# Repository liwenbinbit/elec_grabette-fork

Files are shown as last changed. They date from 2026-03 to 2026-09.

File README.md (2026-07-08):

# "Grabette"/"Gripette" Electronic Boards

This repository is part of the ["Grabette" project](https://github.com/pollen-robotics/grabette). It gathers several small PCBs of Grabette/Gripette. 

## Grabette
Grapette is the data acquisition side.

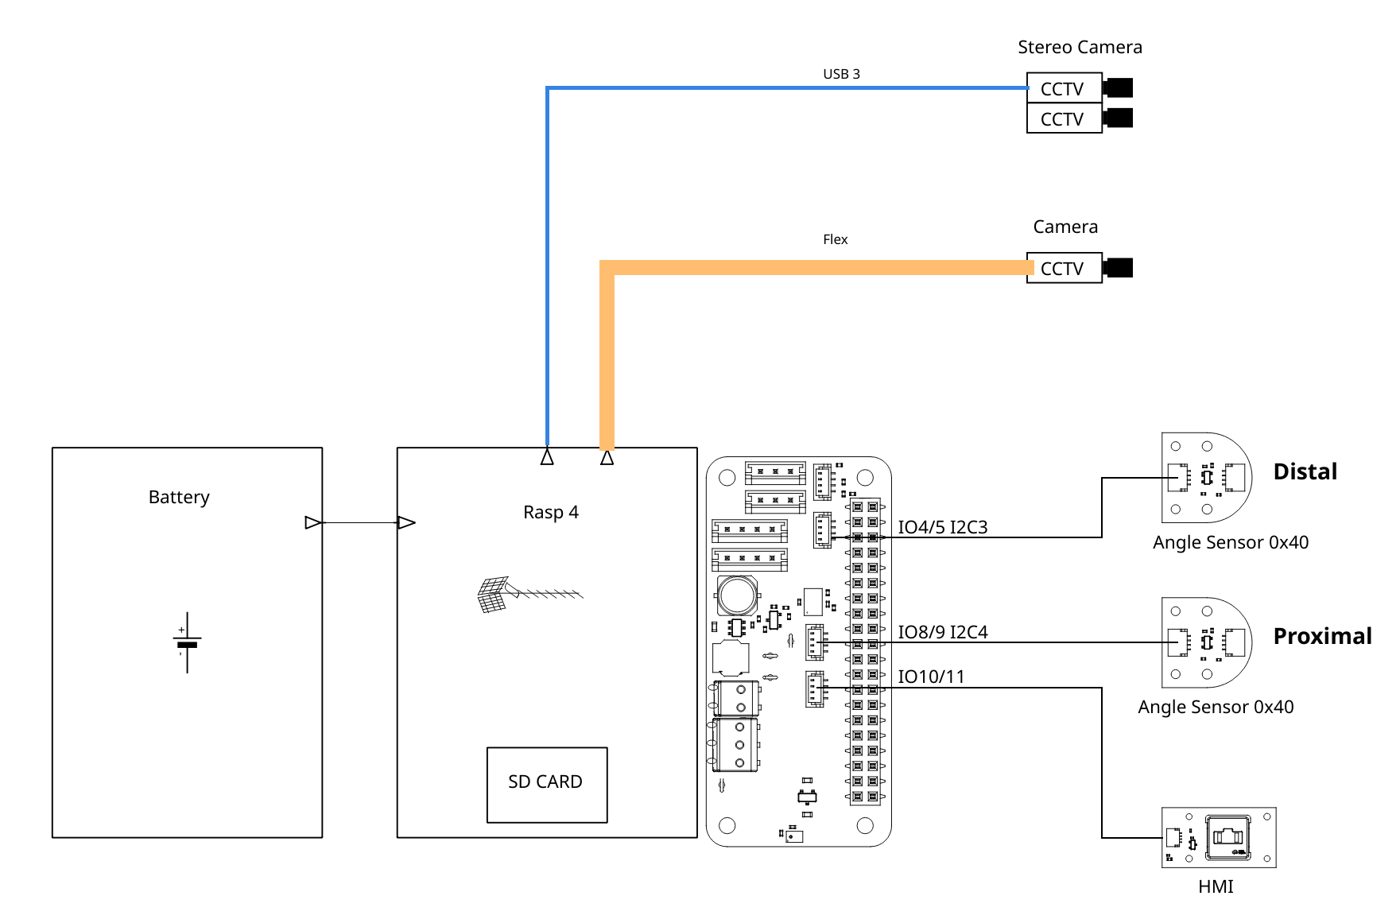
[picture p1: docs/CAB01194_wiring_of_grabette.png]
grabette wiring


It is based on a battery-powered Raspberry PI 4 plus a [HAT](https://github.com/pollen-robotics/elec_RPI_Robot_HAT) to which a serie of sensing elements is added. Camera, Stereo Camera, angle sensors, IMU (included on the HAT) and a button + a LED as user interface.

 - angle_sensor

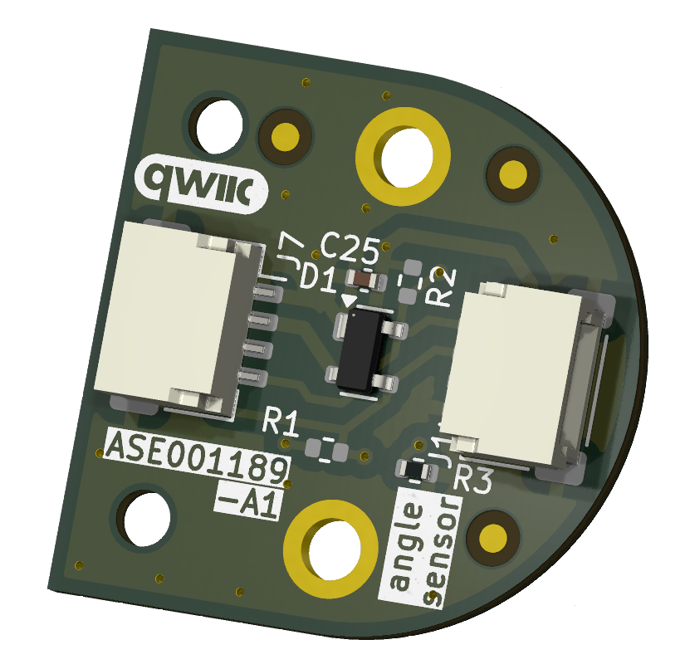
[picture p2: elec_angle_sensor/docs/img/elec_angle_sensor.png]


 - IMU (Not used)

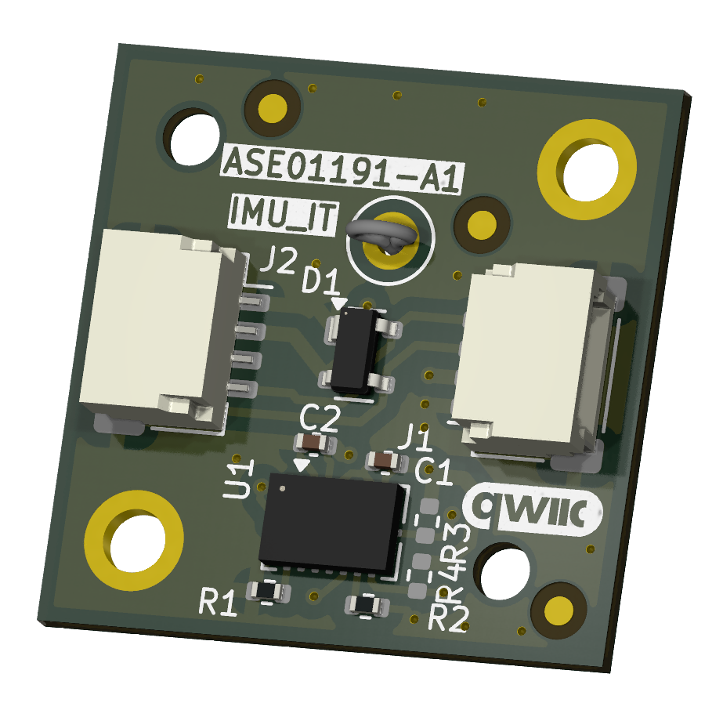
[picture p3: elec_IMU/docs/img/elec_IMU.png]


 - HMI

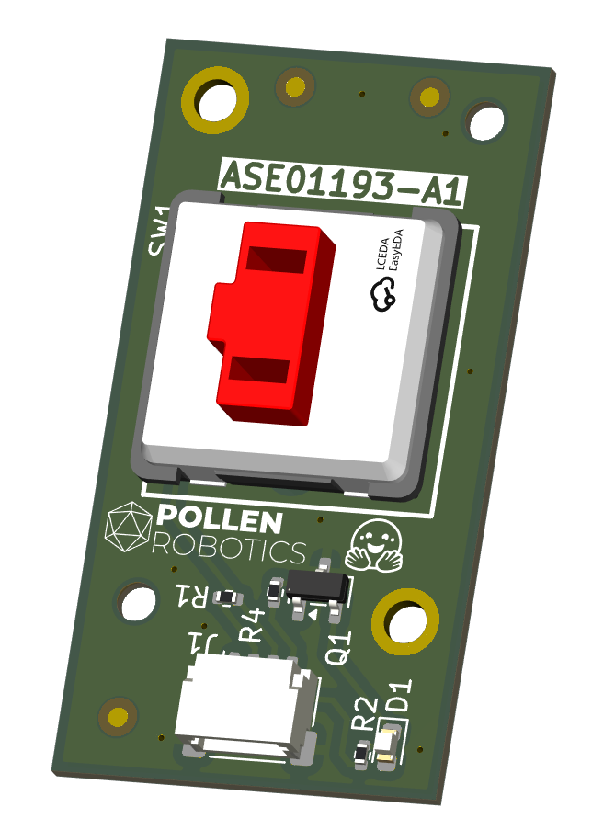
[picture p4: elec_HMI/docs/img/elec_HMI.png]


## Gripette
Gripette is the actuator side. 

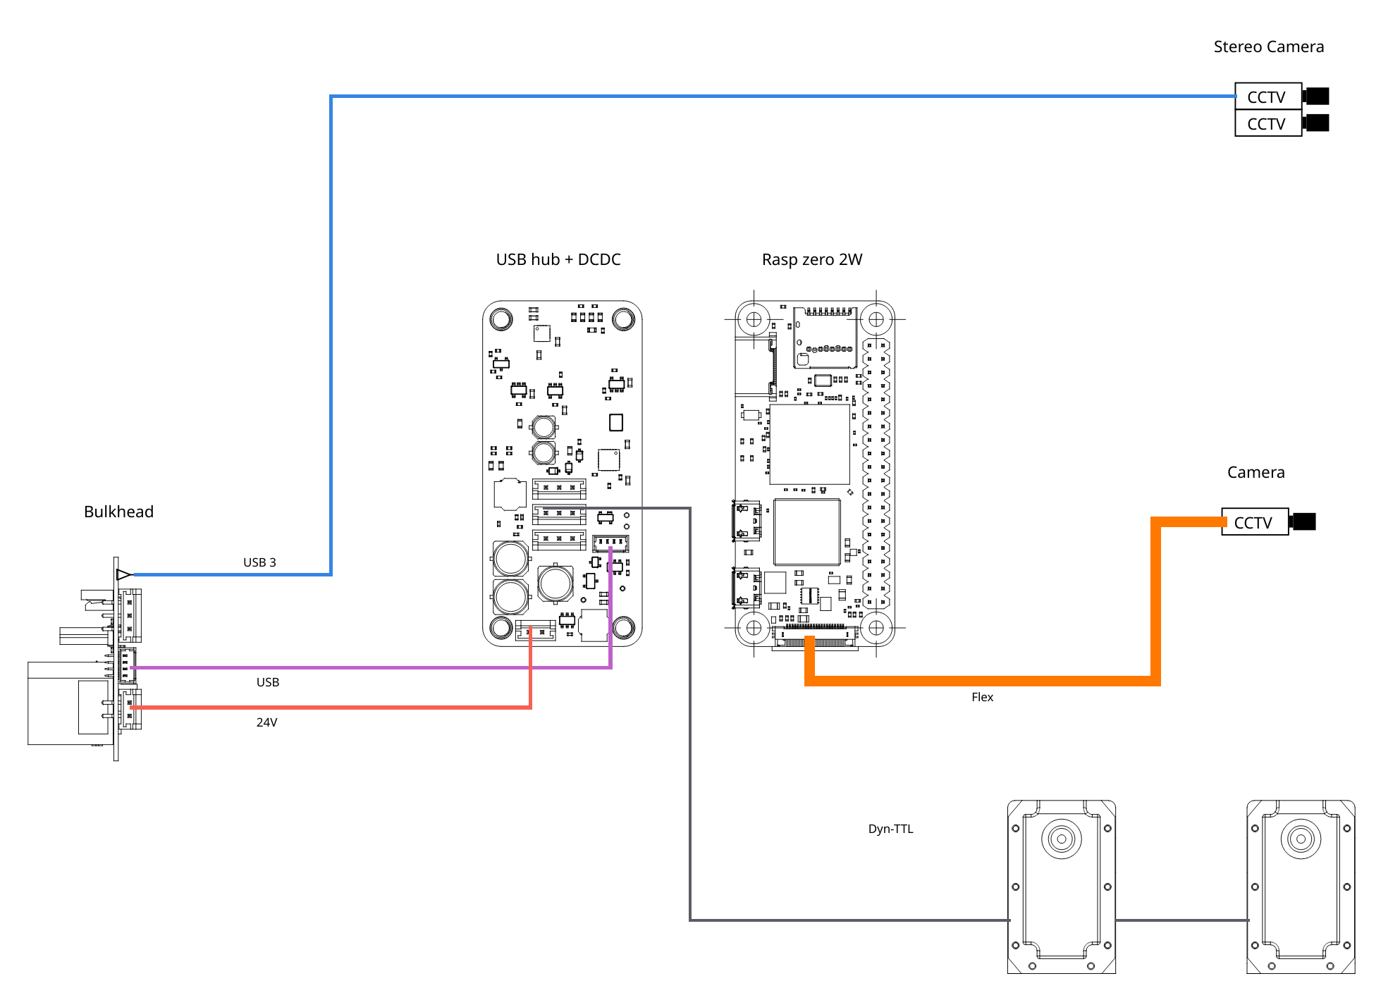
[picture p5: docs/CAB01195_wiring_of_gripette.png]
gripette wiring


It also gathers data with the same Camera/Stereo Camera system and drive motors. The "under-HAT" electronic board is associated to a Raspberry PI zero 2W. It has a interface to the motors (now Feetech wiring). A Bulk-head board makes the mechanical interface with the arm that holds Gripette.

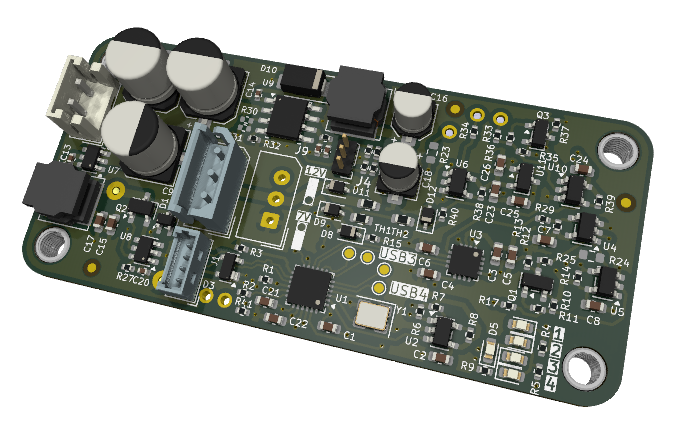
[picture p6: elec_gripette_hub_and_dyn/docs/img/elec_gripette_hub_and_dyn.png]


Bulk-head:

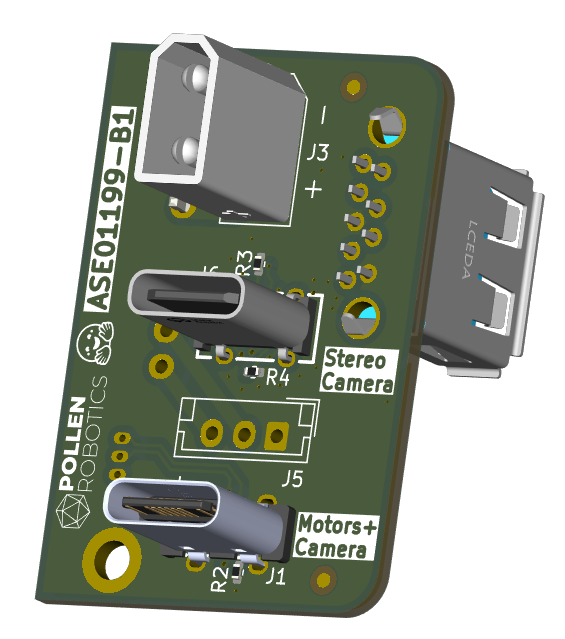
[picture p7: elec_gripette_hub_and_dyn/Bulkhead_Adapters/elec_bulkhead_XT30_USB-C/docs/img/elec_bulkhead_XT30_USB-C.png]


## Basically
 - Designed with KiCAD 9.

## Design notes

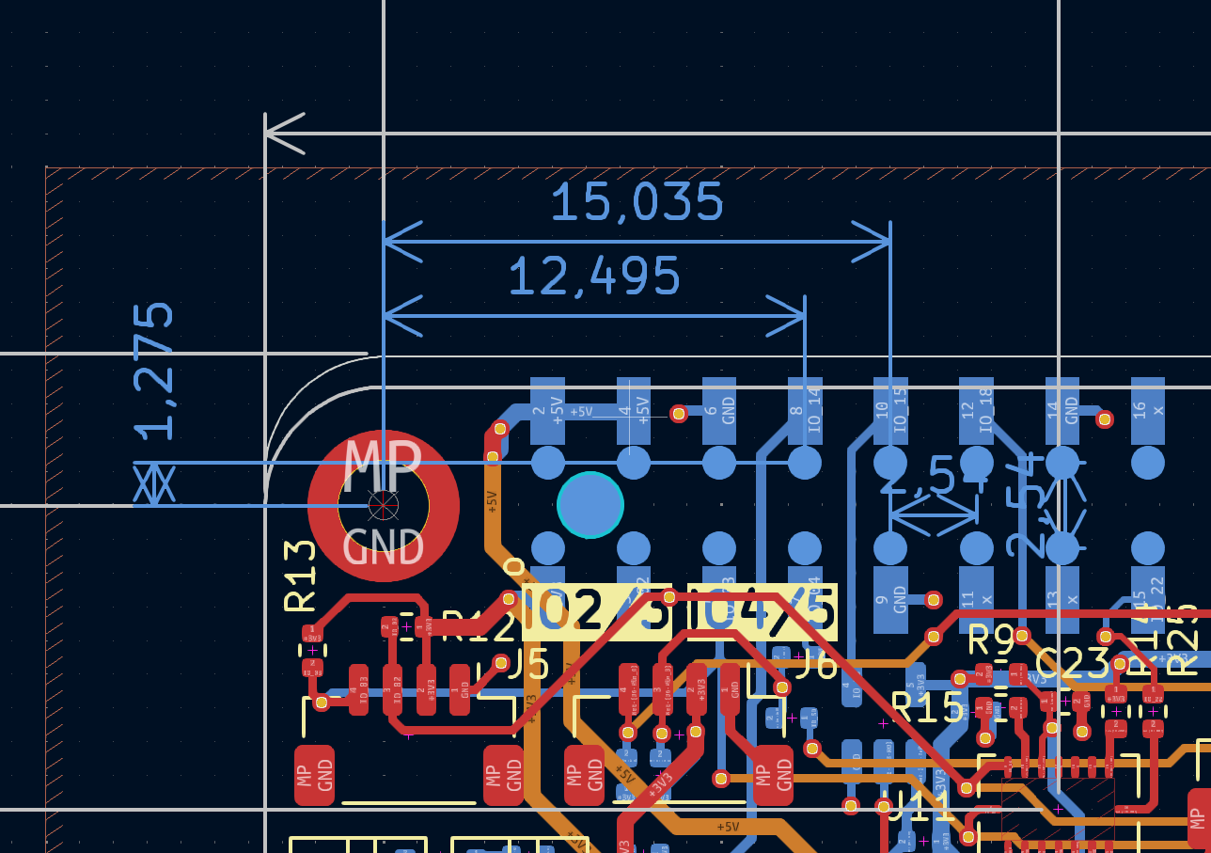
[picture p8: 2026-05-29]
elec_gripette_hub_and_dyn/docs/extra_pogo-pins_positions.png

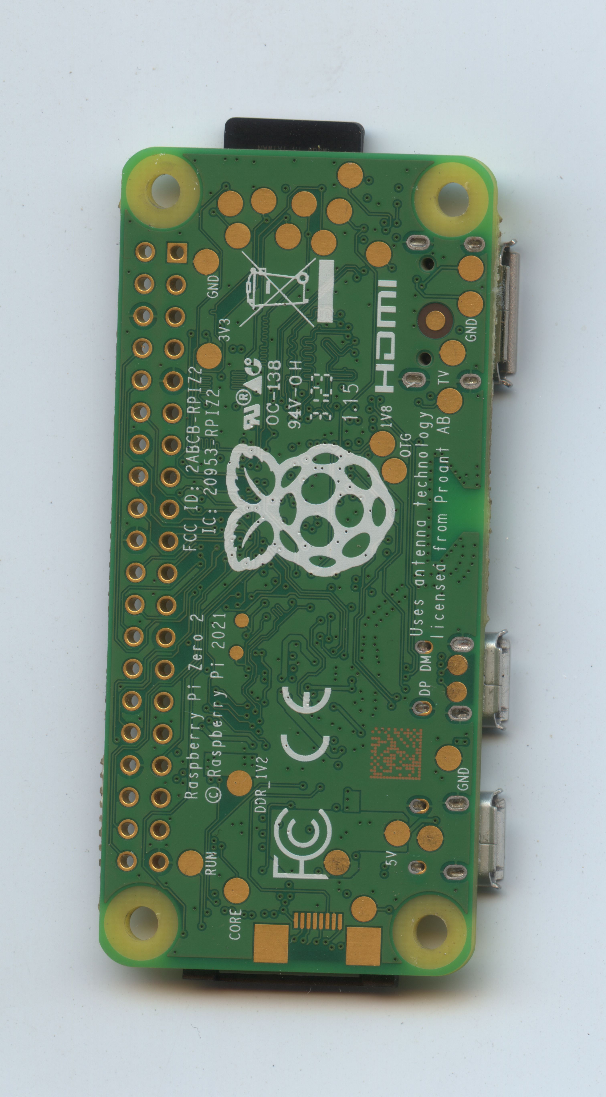
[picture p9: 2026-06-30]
elec_gripette_hub_and_dyn/docs/rasp_zero_2W_bottom.jpg

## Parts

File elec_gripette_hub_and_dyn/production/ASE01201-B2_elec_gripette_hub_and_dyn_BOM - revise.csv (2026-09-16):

Designator | Footprint | Quantity | Value | LCSC Part #
C1 | 0603 | 1 | 10u | C1691
C10, C11, C9 | CP_Elec_6.3x7.7 | 3 | 10u 35V | C72488
C12 | 0402 | 1 | 4n7 | C1518204
C13, C14 | 0402 | 2 | 100n | C307331
C15, C17 | 0603 | 2 | 22u 6V3 | C84419
C16, C18 | CP_Elec_4x5.4 | 2 | 22u 16V | C72502
C19 | 0402 | 1 | 47p | C1567
C2, C21, C22, C23, C24, C4, C6, C7, C8 | 0603 | 9 | 100n | C85864
C20 | 0402 | 1 | 100n 6V3 | C1525
C25, C26, C3, C5 | 0603 | 4 | 1u | C1592
C27 | 0805 | 1 | 3,3u 35V | C361184
D1 | SOT-323_SC-70 | 1 | BAT54W | C78606
D10 | D_SMA | 1 | D_Schottky 3A | C8678
D11, D9 | D_SOD-323 | 2 | B5819WS | C64886
D12, D8 | D_SOD-323 | 2 | 5V1 | C151348
D2, D4, D6, D7 | 0603 | 4 | LED_Small | C7429915
D3 | SOT-143 | 1 | SP0503BAHT | C41364459
D5 | 0603 | 1 | LED_Small | C19171301
H4, H5, H6, H7 | SMD_BD5.6-D4.1_spacer | 4 | M2,5 x 4mm spacer | C2916324
J1 | Molex_PicoBlade_53047-0410_1x04_P1.25mm_Vertical | 1 | pico4 | C504989
J10, J13, J14 | CONN-TH_YZ95315064P-01_pogo | 3 | Pogo-pin 4mm | C5157245
J2 | JST_EH_B2B-EH-A_1x02_P2.50mm_Vertical | 1 | JST EH 2 | C160262
J4 | PinHeader_1x03_P1.27mm_Vertical | 1 | Header 3 | C7470079
J5 | Molex_SPOX_5267-03A_1x03_P2.50mm_Vertical | 1 | Feetech | C293315
J7, J8 | CONN-TH_YZ08415060P-02_pogo | 2 | Pogo-pin 2A 4mm | C7471674
L1, L2 | L_Bourns_SRN6045TA | 2 | 6,8u 3A | C57254
Q1, Q3 | SOT-23 | 2 | MMBT3906 | C727128
Q2 | TSOT-23 | 1 | SI2312CDS-T1-GE3 | C142518
R1, R10, R11, R13, R14, R35, R36, R38, R39, R8 | 0402 | 10 | 10k | C25744
R12, R37 | 0402 | 2 | 20k | C2906867
R15, R40 | 0402 | 2 | 150R | C138054
R16 | 0402 | 1 | 100k | C2906883
R17, R2, R25, R29, R33, R34, R41 | 0402 | 7 | 0R | C17168
R18 | 0402 | 1 | 16k9 | C25858
R21 | 0402 | 1 | 62k | C2909375
R22 | 0402 | 1 | 8k2 | C25924
R26 | 0402 | 1 | 7k5 | C25918
R27 | 0402 | 1 | 100R | C2906860
R28 | 0603 | 1 | 0R | C21189
R3 | 0402 | 1 | 2k7 | C138017
R32 | 0402 | 1 | 243k | C43249
R4, R5, R9 | 0402 | 3 | 330R | C105875
R6, R7 | 0402 | 2 | 5k1 | C25905
TH1, TH2 | 0603 | 2 | 100R thermistor | C913703
U1 | WQFN-24-1EP_4x4mm_P0.5mm_EP2.6x2.6mm | 1 | FE1.1s_24-Pin_WQFN | C6776948
U10, U5 | SOT-23-5 | 2 | SN74LVC1G126DBVR | C7834
U11 | SOT-23 | 1 | MCP1700x-330xxTT | C39051
U2 | SOT-23-5 | 1 | 24C02S | C18723540
U3 | WCH_QFN-16-1EP_3x3mm_P0.5mm_EP1.8x1.8mm | 1 | CH343P | C2846043
U4, U6 | SOT-23-5 | 2 | SN74LVC1G125DBV | C23654
U7 | TSOT-23-6 | 1 | AP63205 | C2071056
U8 | TSOT-23-6 | 1 | LM5050-1 | C473393
U9 | Texas_R-PDSO-G8_EP2.95x4.9mm_Mask2.4x3.1mm_ThermalVias | 1 | TPS54560BDDA | C1850354
Y1 | Crystal_SMD_3225-4Pin_3.2x2.5mm | 1 | 12MHz | C133334

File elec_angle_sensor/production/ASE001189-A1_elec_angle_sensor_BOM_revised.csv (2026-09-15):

Designator | Footprint | Quantity | Value | LCSC Part #
C25 | 402 | 1 | 100n | C307331
D1 | SOT-143 | 1 | SP0503BAHT | C41364459
J1 | JST_SH_SM04B-SRSS-TB_1x04-1MP_P1.00mm_Horizontal | 1 | JST SH | C160404
J7 | JST_SH_SM04B-SRSS-TB_1x04-1MP_P1.00mm_Horizontal | 1 | JST SH | C160404
R3 | 402 | 1 | 0R | C17168
U1 | SOIC-8_3.9x4.9mm_P1.27mm | 1 | AS5600L | C2153666

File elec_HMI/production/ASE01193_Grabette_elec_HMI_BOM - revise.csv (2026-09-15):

Designator | Footprint | Quantity | Value | LCSC Part #
D1 | 0603 | 1 | Red | C84263
J1 | JST_SH_SM04B-SRSS-TB_1x04-1MP_P1.00mm_Horizontal | 1 | JST SH | C160404
Q1 | SOT-23 | 1 | MMBT3906 | C727128
R1 | 0402 | 1 | 10k | C25744
R2, R4 | 0402 | 2 | 470R | C25117
SW1 | SW_Cherry_MX_1.00u_PCB | 1 | SW_SPST | C400229

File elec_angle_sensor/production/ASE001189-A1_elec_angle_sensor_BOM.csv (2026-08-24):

Designator | Footprint | Quantity | Value | LCSC Part #
C25 | 0402 | 1 | 100n | C307331
D1 | SOT-143 | 1 | SP0503BAHT | C41364459
G1 | Logo_qwiic_5mm | 1 | qwiic_Logo
H2 | Logo_HF_2025 | 1 | Logo HF 2025
J1, J7 | JST_SH_SM04B-SRSS-TB_1x04-1MP_P1.00mm_Horizontal | 2 | JST SH | C160404
R1, R2 | 0402 | 2 | DNP-10k | C25744
R3 | 0402 | 1 | 0R | C17168
U1 | SOIC-8_3.9x4.9mm_P1.27mm | 1 | AS5600L | C2153666

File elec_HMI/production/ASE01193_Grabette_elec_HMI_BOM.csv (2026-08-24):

Designator | Footprint | Quantity | Value | LCSC Part #
D1 | 0603 | 1 | Red | C84263
H2 | Logo_HF_2025 | 1 | Logo HF 2025
J1 | JST_SH_SM04B-SRSS-TB_1x04-1MP_P1.00mm_Horizontal | 1 | JST SH | C160404
Q1 | SOT-23 | 1 | MMBT3906 | C727128
R1 | 0402 | 1 | 10k | C25744
R2, R4 | 0402 | 2 | 470R | C25117
SW1 | SW_Cherry_MX_1.00u_PCB | 1 | SW_SPST | C400229

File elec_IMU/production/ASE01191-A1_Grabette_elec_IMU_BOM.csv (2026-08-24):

Designator | Footprint | Quantity | Value | LCSC Part #
C1, C2 | 0402 | 2 | 100n 6V3 | C1525
D1 | SOT-143 | 1 | SP0503BAHT | C41364459
G1 | Logo_qwiic_5mm | 1 | qwiic_Logo
H2 | Logo_HF_2025 | 1 | Logo HF 2025
J1, J2 | JST_SH_SM04B-SRSS-TB_1x04-1MP_P1.00mm_Horizontal | 2 | JST SH | C160404
R1, R2 | 0402 | 2 | 0R | C17168
R3, R4 | 0402 | 2 | DNP-10k | C25744
TP1 | TestPoint_Loop_D2.50mm_Drill1.0mm_LowProfile | 1 | TestPoint
U1 | Bosch_LGA-16_4.5x3mm_P0.5mm_LayoutBorder7x1y_ClockwisePinNumbering | 1 | BMI088 | C194919

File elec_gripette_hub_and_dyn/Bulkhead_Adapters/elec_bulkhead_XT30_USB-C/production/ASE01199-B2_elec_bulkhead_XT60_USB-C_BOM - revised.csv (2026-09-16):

Designator | Footprint | Quantity | Value | LCSC Part #
J1 | USB-C_16p_vert_Shou-Han_TYPE-C 16P LTH6.8 - C5187468 | 1 | USB-C Rec. Vert. | C5187468
J2 | JST_EH_S2B-EH_1x02_P2.50mm_Horizontal | 1 | JST EH 2 | C514173
J3 | AMASS_XT30UPB-M_1x02_P5.0mm_Vertical | 1 | XT30 | C428721
J4 | Molex_PicoBlade_53048-0410_1x04_P1.25mm_Horizontal | 1 | pico4 | C588275
J6 | USB-C_TYPE-C-24PLT-H10.5-1 | 1 | USB_C_Receptacle | C3151750
J8 | USB-A-TH_MOLEX_484080003 | 1 | USB3_A | C587839
R1, R2, R3, R4 | 0402 | 4 | 5k1 | C25905

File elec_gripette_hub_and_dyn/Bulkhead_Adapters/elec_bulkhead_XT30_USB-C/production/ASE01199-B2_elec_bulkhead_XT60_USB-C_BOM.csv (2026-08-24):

Designator | Footprint | Quantity | Value | LCSC Part #
H2 | Logo_HF_2025 | 1 | Logo HF 2025
J1 | USB-C_16p_vert_Shou-Han_TYPE-C 16P LTH6.8 - C5187468 | 1 | USB-C Rec. Vert. | C5187468
J2 | JST_EH_S2B-EH_1x02_P2.50mm_Horizontal | 1 | JST EH 2 | C514173
J3 | AMASS_XT30UPB-M_1x02_P5.0mm_Vertical | 1 | XT30 | C428721
J4 | Molex_PicoBlade_53048-0410_1x04_P1.25mm_Horizontal | 1 | pico4 | C588275
J5 | JST_EH_B3B-EH-A_1x03_P2.50mm_Vertical | 1 | DNP - Dynamixel-3 | C160259
J6 | USB-C_TYPE-C-24PLT-H10.5-1 | 1 | USB_C_Receptacle | C3151750
J8 | USB-A-TH_MOLEX_484080003 | 1 | USB3_A | C587839
J9 | JST_EH_S3B-EH_1x03_P2.50mm_Horizontal | 1 | DNP - Dynamixel-3 | C263754
R1, R2, R3, R4 | 0402 | 4 | 5k1 | C25905

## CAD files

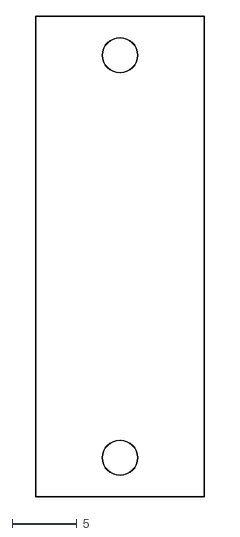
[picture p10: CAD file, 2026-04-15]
elec_gripette_hub_and_dyn/Bulkhead_Adapters/elec_bulkhead_XT30_USB-C/docs/bulkhead.dxf
13.0 x 37.0

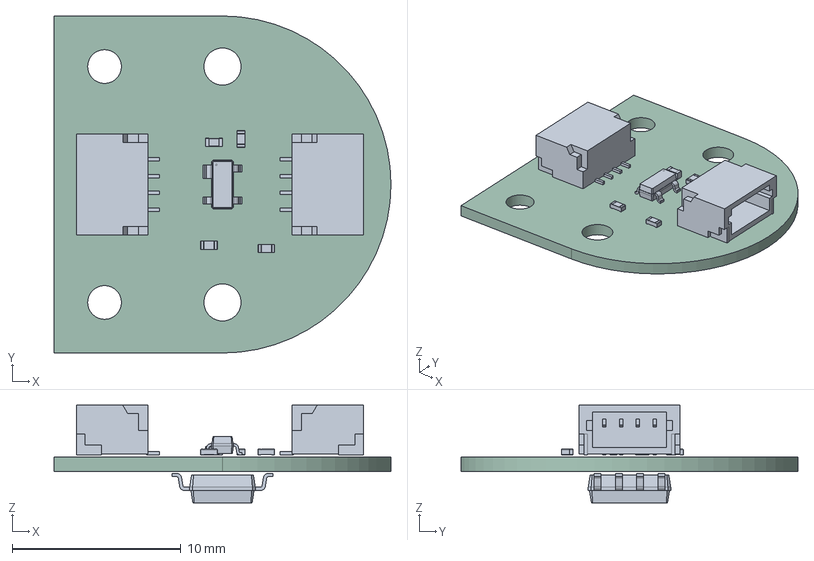
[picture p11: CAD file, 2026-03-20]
elec_angle_sensor/production/ASE001189-A1_elec_angle_sensor_STEP.step
20.0 x 20.0 x 5.79 mm
C_0402_1005Metric
JST_SH_SM04B-SRSS-TB_1x04-1MP_P1.00mm_Horizontal x 2
R_0402_1005Metric x 3
SOT-143
SOIC-8_3.9x4.9mm_P1.27mm
elec_angle_sensor_PCB

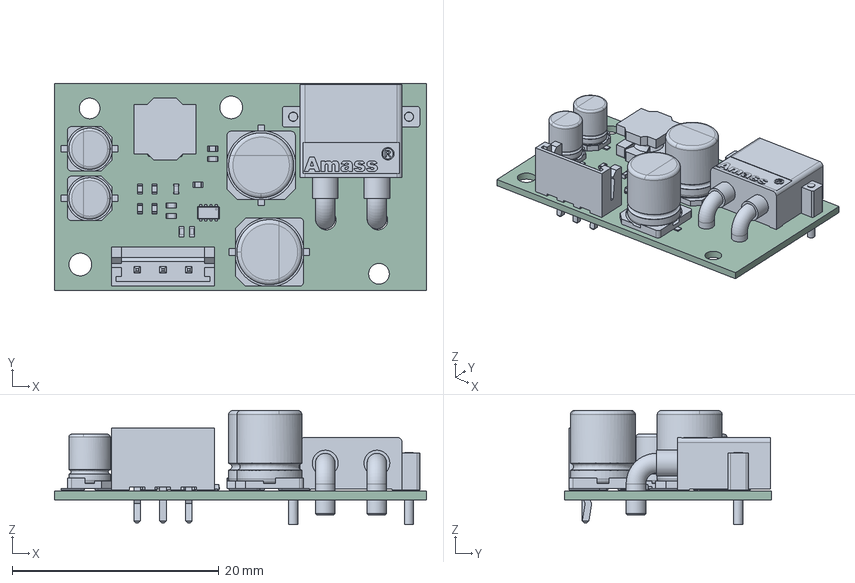
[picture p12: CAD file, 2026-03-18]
elec_DCDC/fab/ASE01197_elec_DCDC.step
36.0 x 20.0 x 11.1 mm
R_0402_1005Metric x 9
SOT-583-8_L2.1-W1.2-P0.50-LS1.6-BR
CP_Elec_4x5.4 x 2
C_0402_1005Metric x 3
Amass_XT30PW-M_pcb solder
JST_EH_B3B-EH-A_1x03_P2.50mm_Vertical
CP_Elec_6.3x7.7 x 2
L_Bourns_SRN6045TA
elec_DCDC_PCB

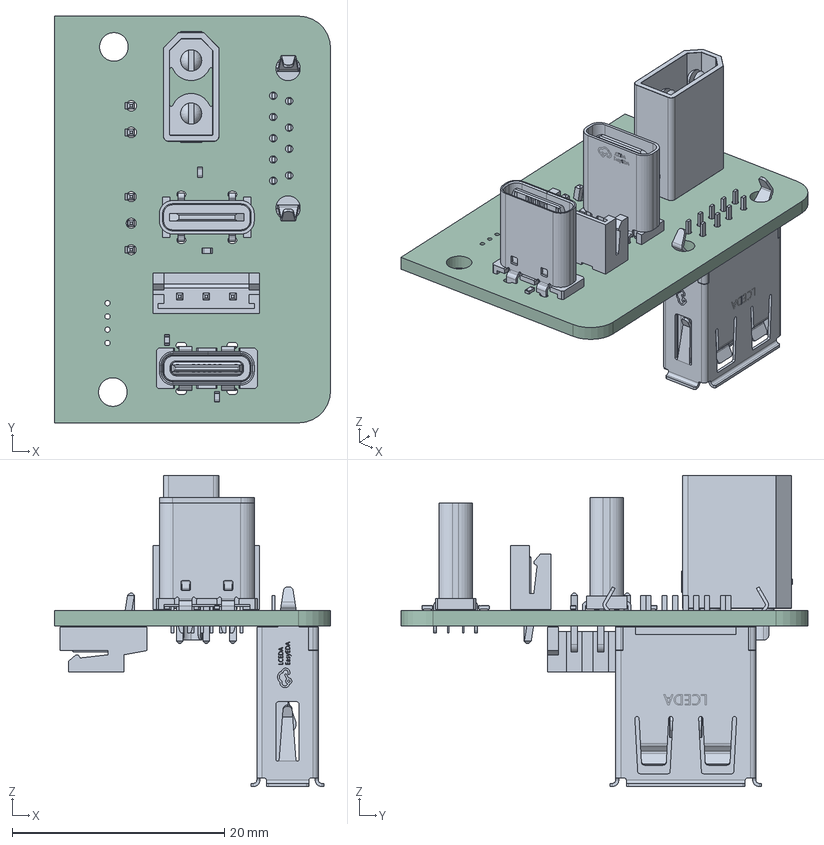
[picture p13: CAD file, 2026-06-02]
elec_gripette_hub_and_dyn/Bulkhead_Adapters/elec_bulkhead_XT30_USB-C/production/ASE01199-B1_elec_bulkhead_XT60_USB-C_STEP.step
26.0 x 38.3 x 29.3 mm
R_0402_1005Metric x 4
JST_EH_B3B-EH-A_1x03_P2.50mm_Vertical
FOO_USB-C_vert
USB-C_TYPE-C-24PLT-H10.5-1
Amass_XT30U_M
USB-A-TH_MOLEX_484080003
JST_EH_S3B-EH_1x03_P2.50mm_Horizontal
JST_EH_S2B-EH_1x02_P2.50mm_Horizontal
elec_bulkhead_XT60_USB-C_PCB

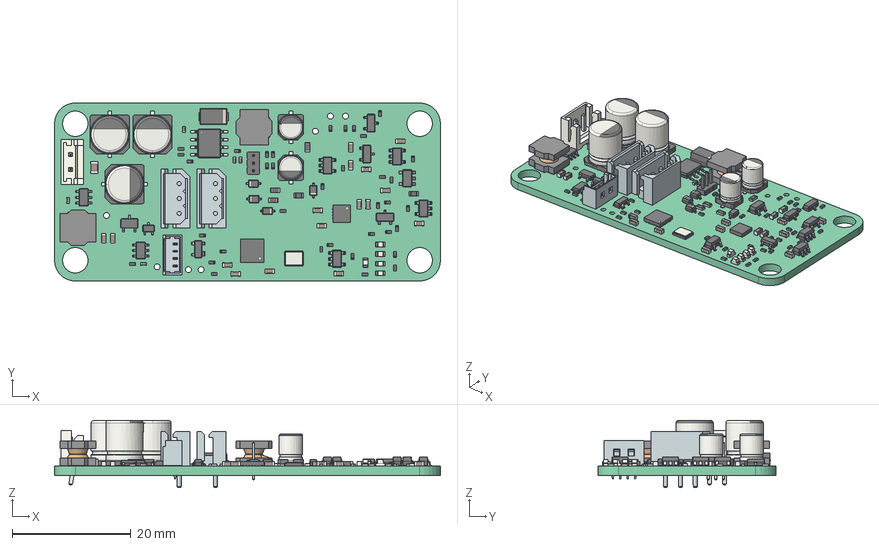
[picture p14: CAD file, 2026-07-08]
elec_gripette_hub_and_dyn/production/ASE01201-B2_elec_gripette_hub_and_dyn_STEP.step
65.0 x 30.0 x 11.3 mm
Local_CS_4c35
Pcb_4c35
PCB_Sketch_4c35
C24_C_0603_1608Metric_0b12b6d945ad x 16
J4_PinHeader_1x03_P127mm_Vertical_d0b1d97bf511
R21_R_0402_1005Metric_38d3d76b5750 x 36
C12_C_0402_1005Metric_682991d83cec x 5
J5_22035035wbm000_01_a64ff34f0dda x 2
U11_SOT-23_a04db7c55f55 x 3
D1_SOT-323_SC-70_295ee537f41e
C10_CP_Elec_63x77_78ab98c25c1e x 3
D10_D_SMA_a0cd4268b988
U2_SOT-23-5_3df24cab8754 x 5
J2_JST_B2B_EH_A_f175109f276f
U7_TSOT-23-6_d955bce0ccf0 x 2
R24_R_0603_1608Metric_f9182ad27e56 x 5
C27_C_0805_2012Metric_3a36ccf0a69e
D3_SOT-143_1b199c003f9f
L2_L_Bourns_SRN6045TA_66351089c577 x 2
Y1_Crystal_SMD_3225-4Pin_3.2x2.5mm_01a24c7c70d7
C16_CP_Elec_4x54_022cea10a9cb x 2
U1_Texas_RTW_WQFN-24-1EP_4x4mm_P0.5mm_EP2.7x2.7mm_30aa45833098
D8_D_SOD-323_8da1174c5746 x 4
J1_0530470410_87ad8df9d123
D6_LED_0603_1608Metric_92907605f6d5 x 5
Q2_TSOT-23_0af3d3150de2
U9_HSOP-8-1EP_3.9x4.9mm_P1.27mm_EP2.41x3.1mm_0021593610a3
U3_QFN-16-1EP_3x3mm_Pitch0.5mm_3ed3ad9fc483

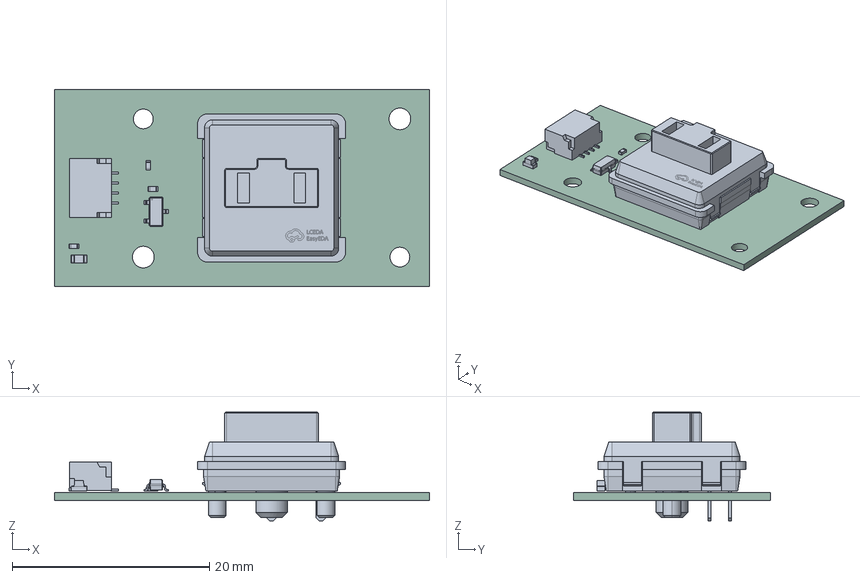
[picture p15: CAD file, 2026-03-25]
elec_HMI/production/ASE01193_Grabette_elec_HMI_STEP.step
38.0 x 20.0 x 11.0 mm
KEY-TH_CPG135001D0X
R_0402_1005Metric x 3
LED_0603_1608Metric
JST_SH_SM04B-SRSS-TB_1x04-1MP_P1.00mm_Horizontal
SOT-23
elec_HMI_PCB

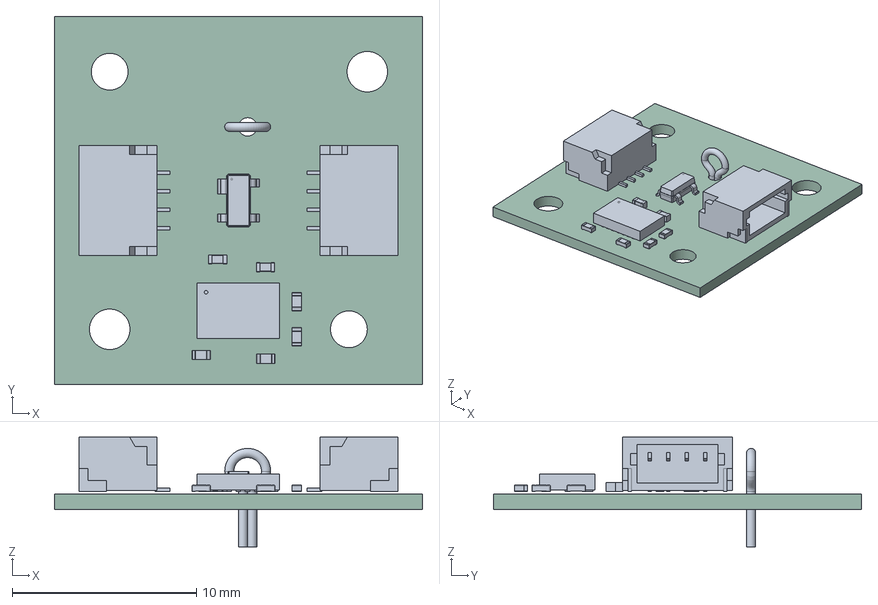
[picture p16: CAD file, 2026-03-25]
elec_IMU/production/ASE01191-A1_Grabette_elec_IMU_STEP.step
20.0 x 20.0 x 5.96 mm
R_0402_1005Metric x 4
TestPoint_Loop_D2.50mm_Drill1.0mm_LowProfile
C_0402_1005Metric x 2
SOT-143
JST_SH_SM04B-SRSS-TB_1x04-1MP_P1.00mm_Horizontal x 2
Bosch_LGA-16_4.5x3mm_P0.5mm_LayoutBorder7x1y_ClockwisePinNumbering
elec_IMU_PCB

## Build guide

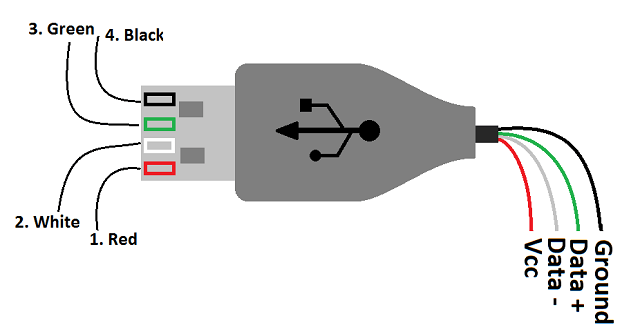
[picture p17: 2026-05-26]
elec_gripette_hub_and_dyn/docs/USB-Wiring-Diagram-2114692425.png

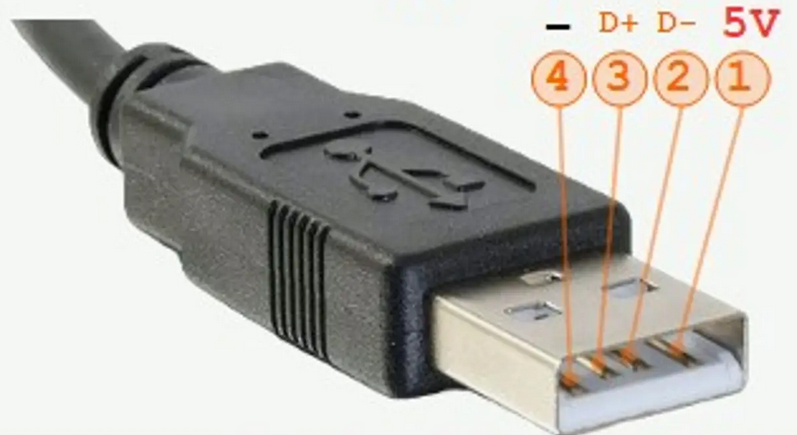
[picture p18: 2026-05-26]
elec_gripette_hub_and_dyn/docs/USB_type_A_wiring.png

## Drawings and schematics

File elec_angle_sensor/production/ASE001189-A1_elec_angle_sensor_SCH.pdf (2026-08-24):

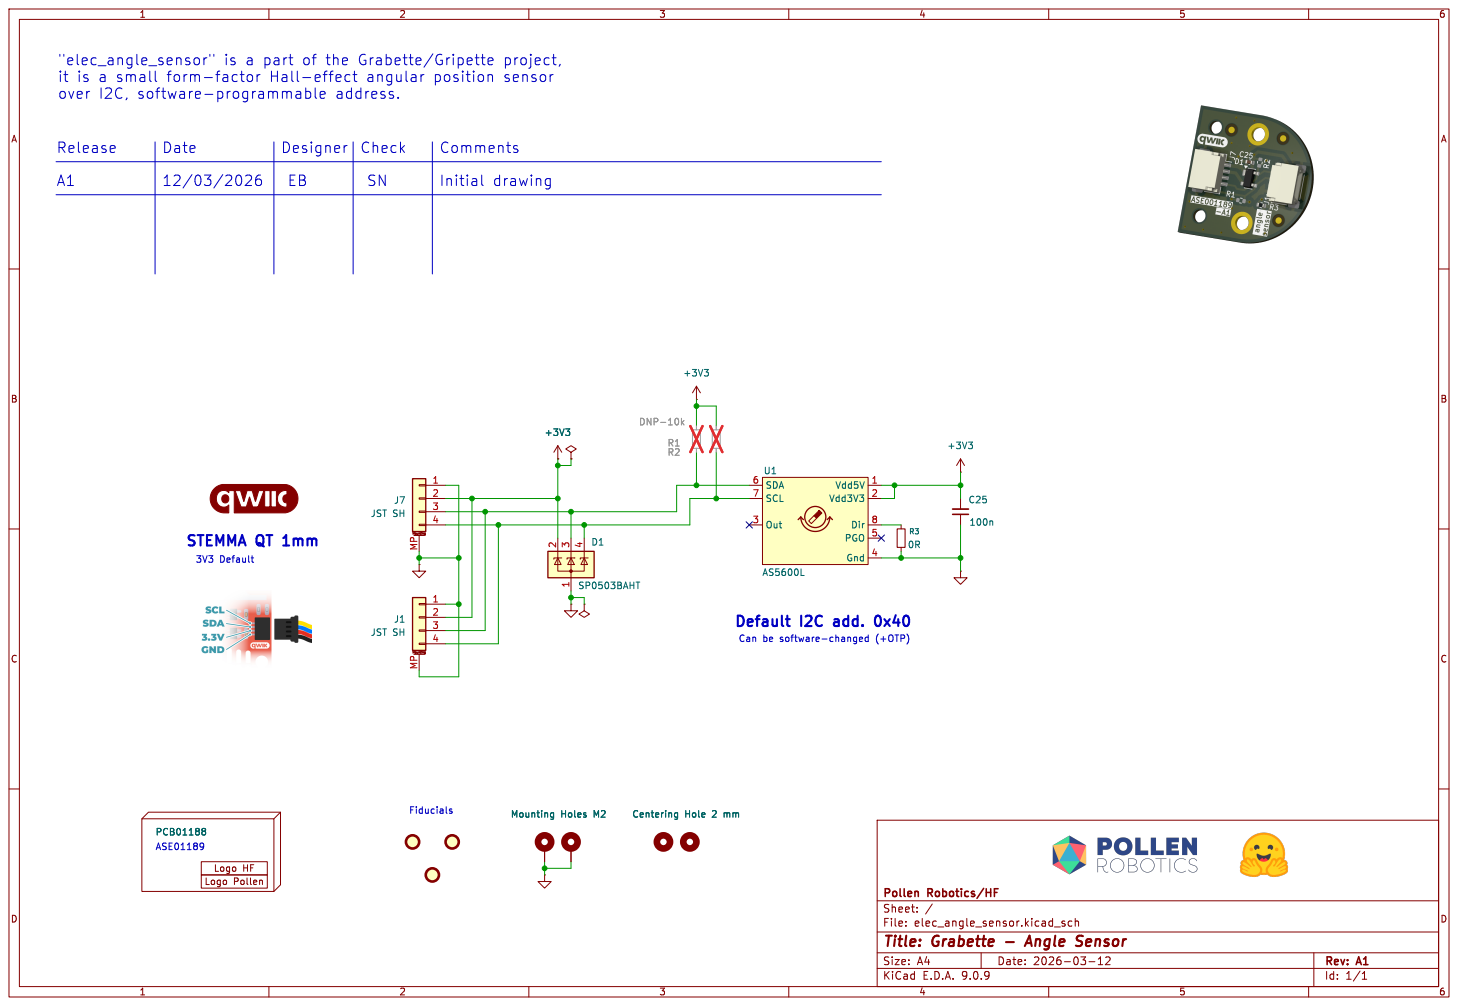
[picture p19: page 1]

Fiducials 3V3 Default STEMMA QT 1mm

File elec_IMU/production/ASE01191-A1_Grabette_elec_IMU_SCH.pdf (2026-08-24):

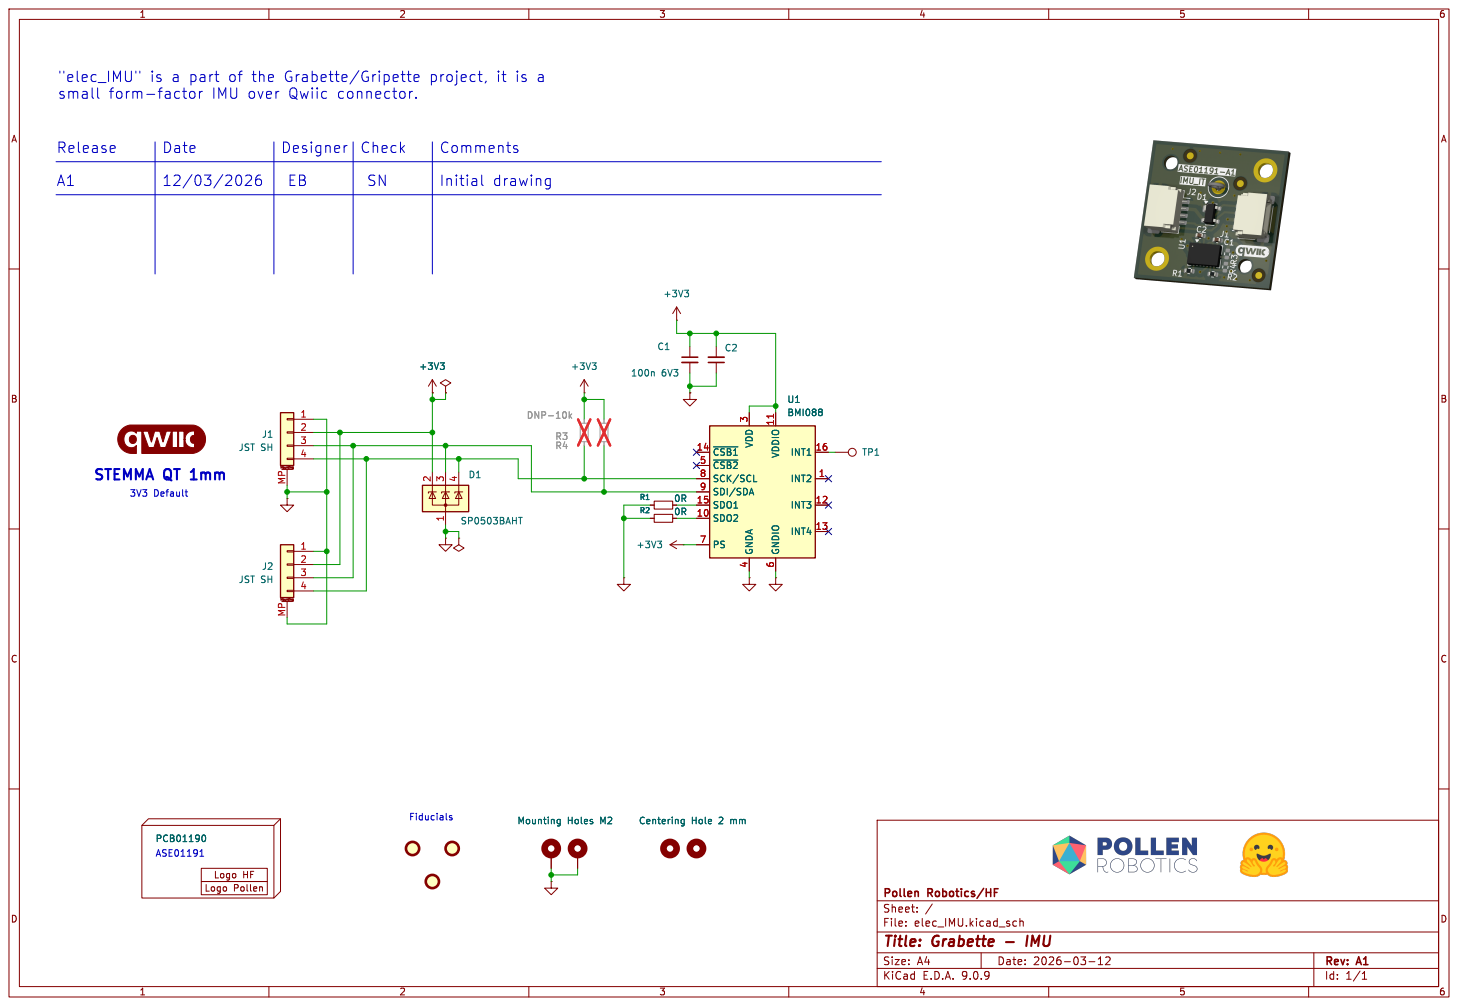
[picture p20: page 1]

Id: 1/1 Title: Grabette - IMU

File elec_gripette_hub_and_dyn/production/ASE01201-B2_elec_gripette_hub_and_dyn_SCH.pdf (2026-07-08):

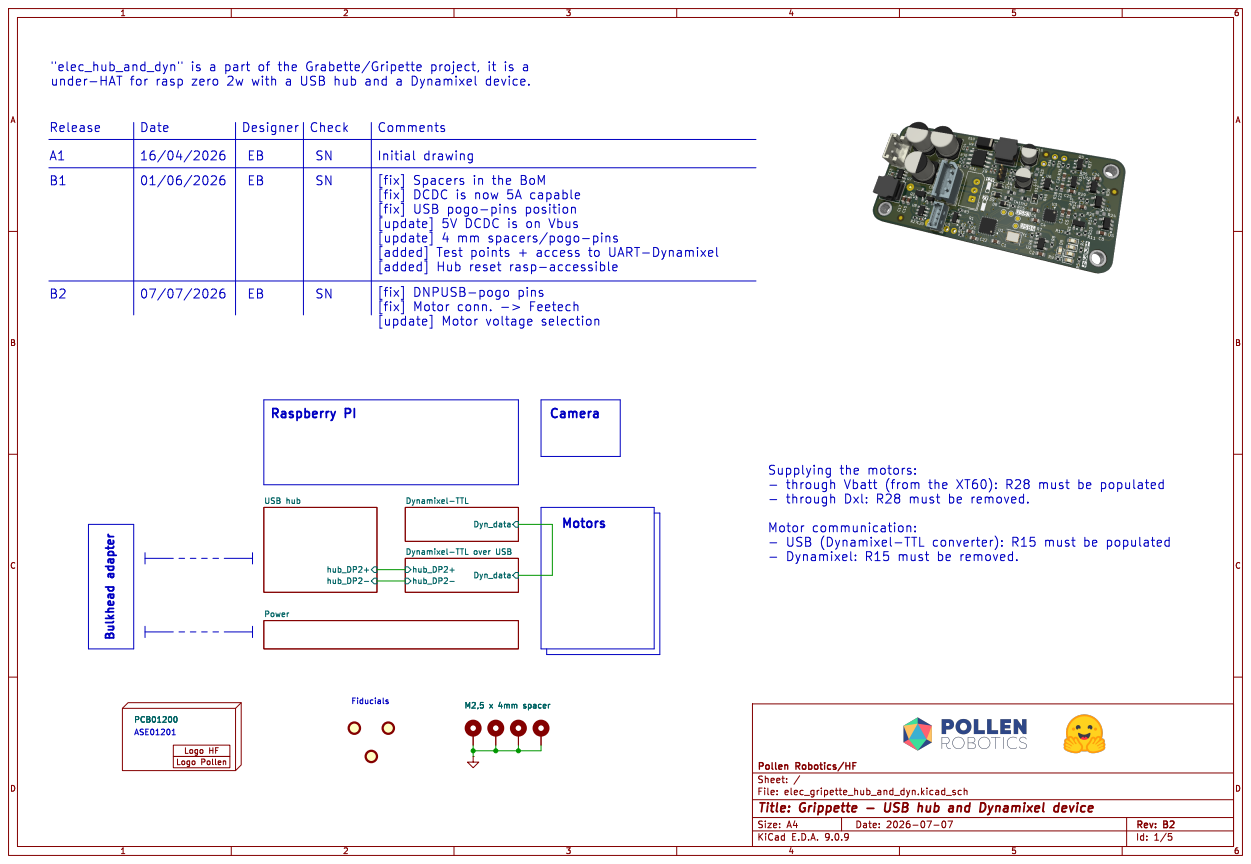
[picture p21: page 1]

Comments
[fix] Spacers in the BoM
[fix] DCDC is now 5A capable
[added] Test points + access to UART-Dynamixel
[added] Hub reset rasp-accessible

16/04/2026 | EB
01/06/2026

Raspberry PI Bulkhead adapter

Id: 1/5 Title: Grippette - USB hub and Dynamixel device

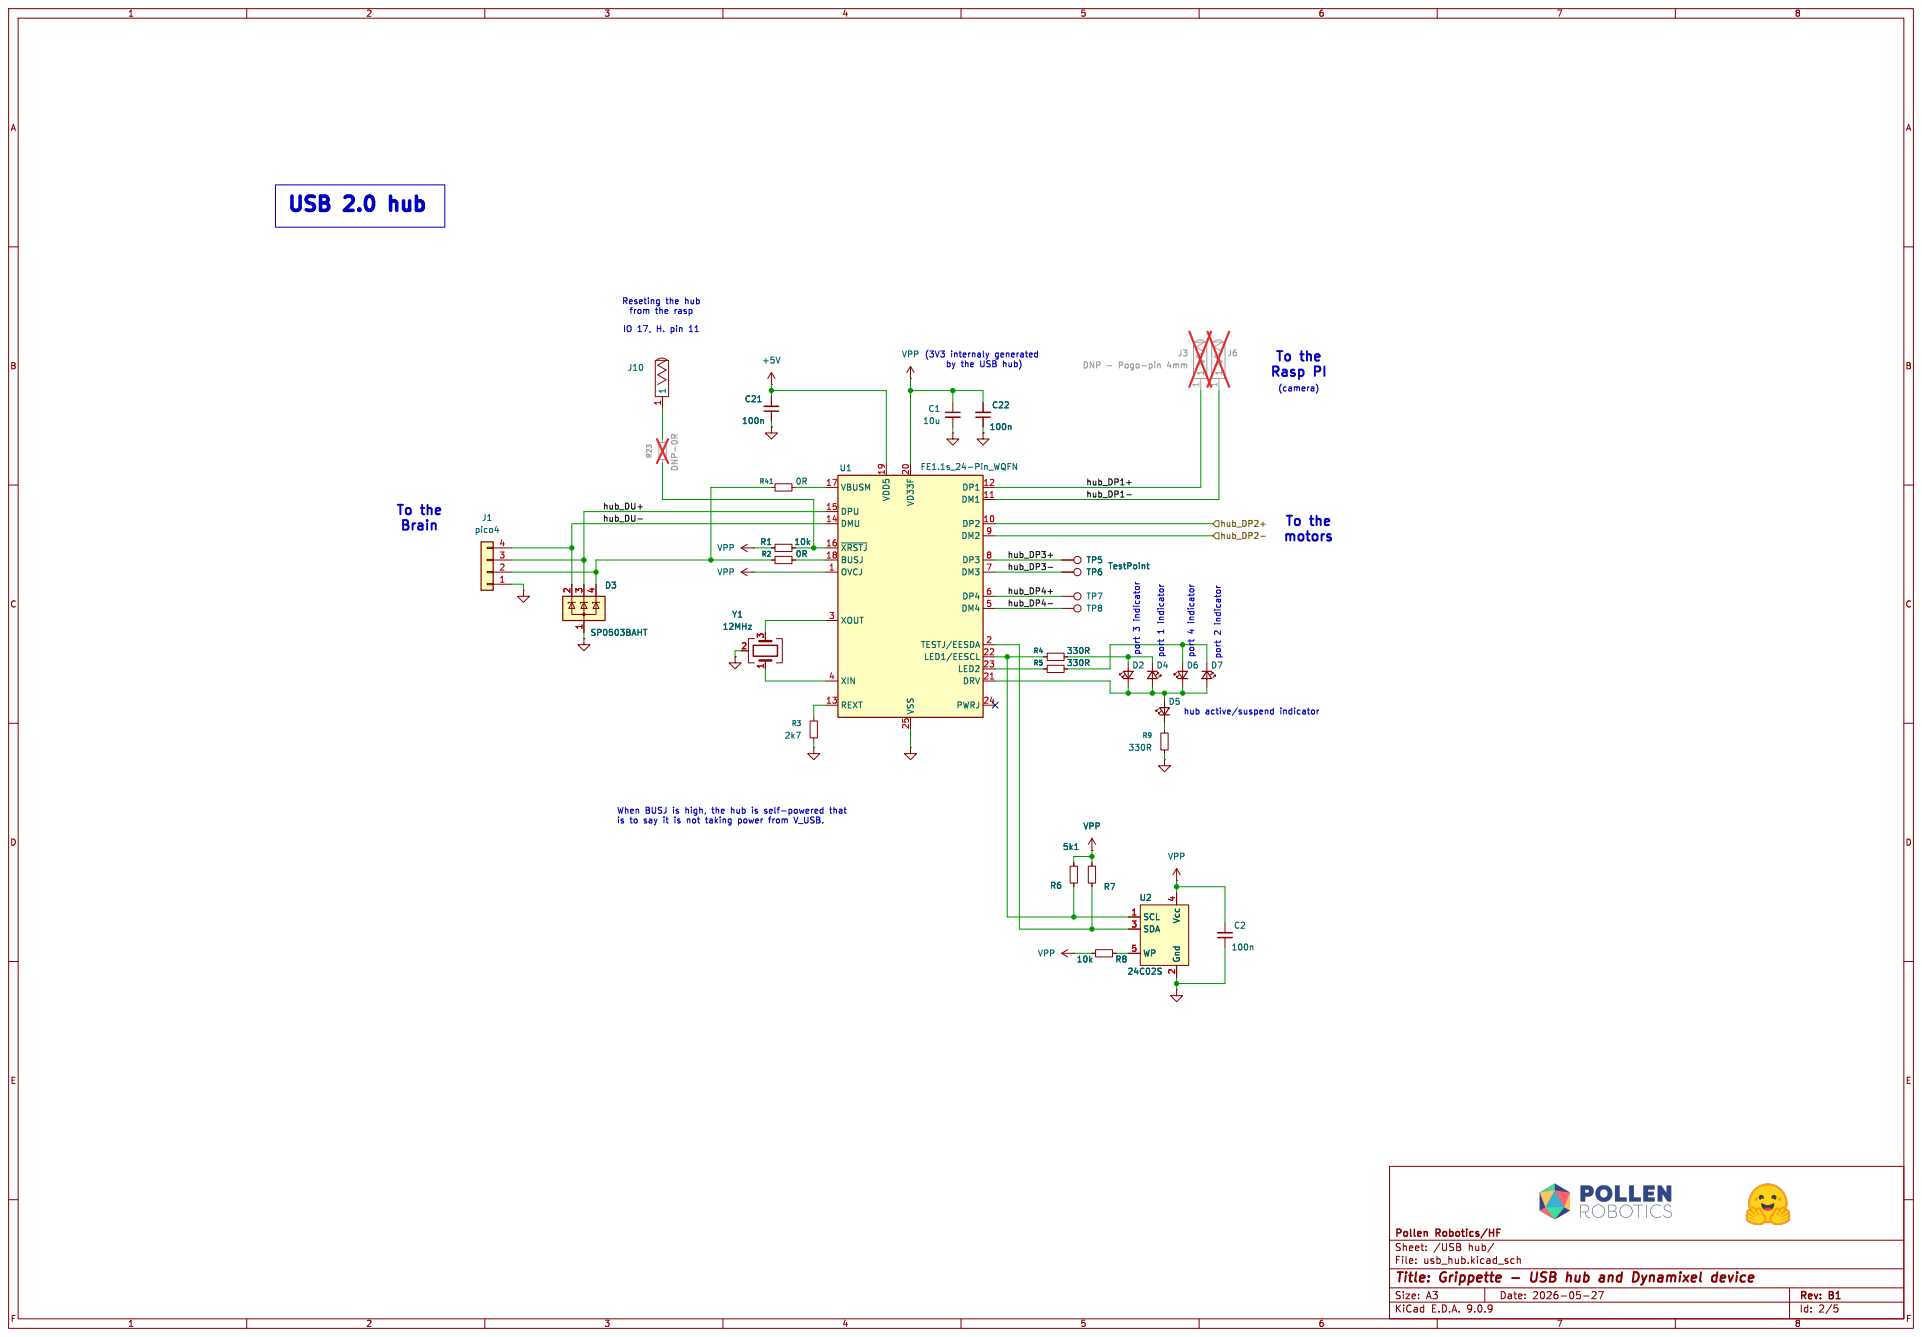
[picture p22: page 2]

Id: 2/5 Title: Grippette - USB hub and Dynamixel device

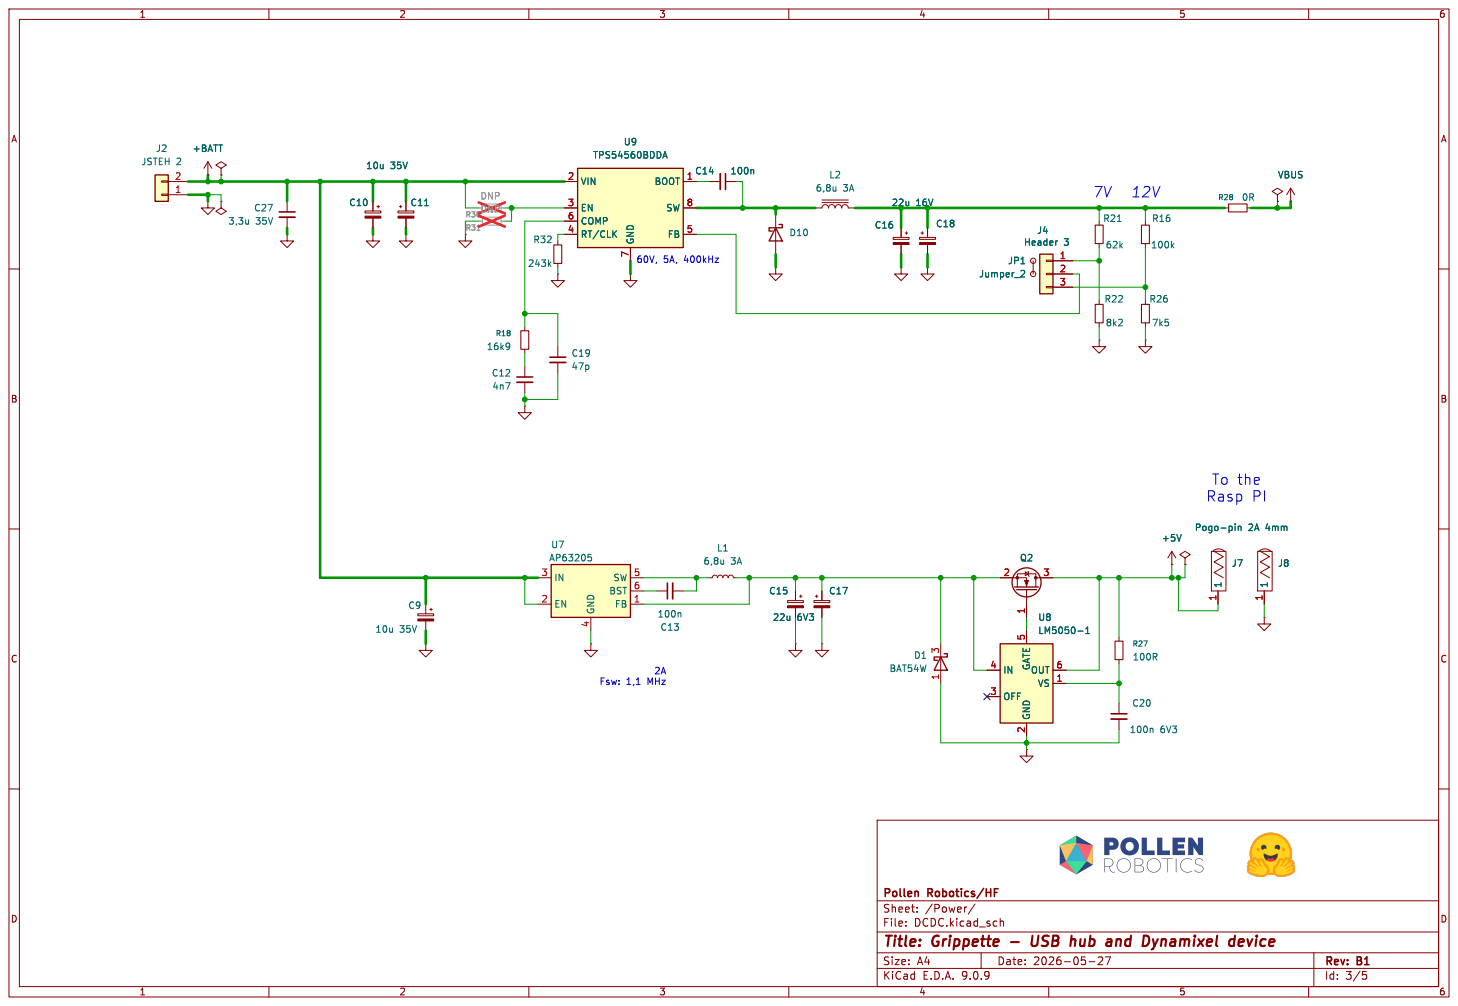
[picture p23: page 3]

Id: 3/5 Title: Grippette - USB hub and Dynamixel device

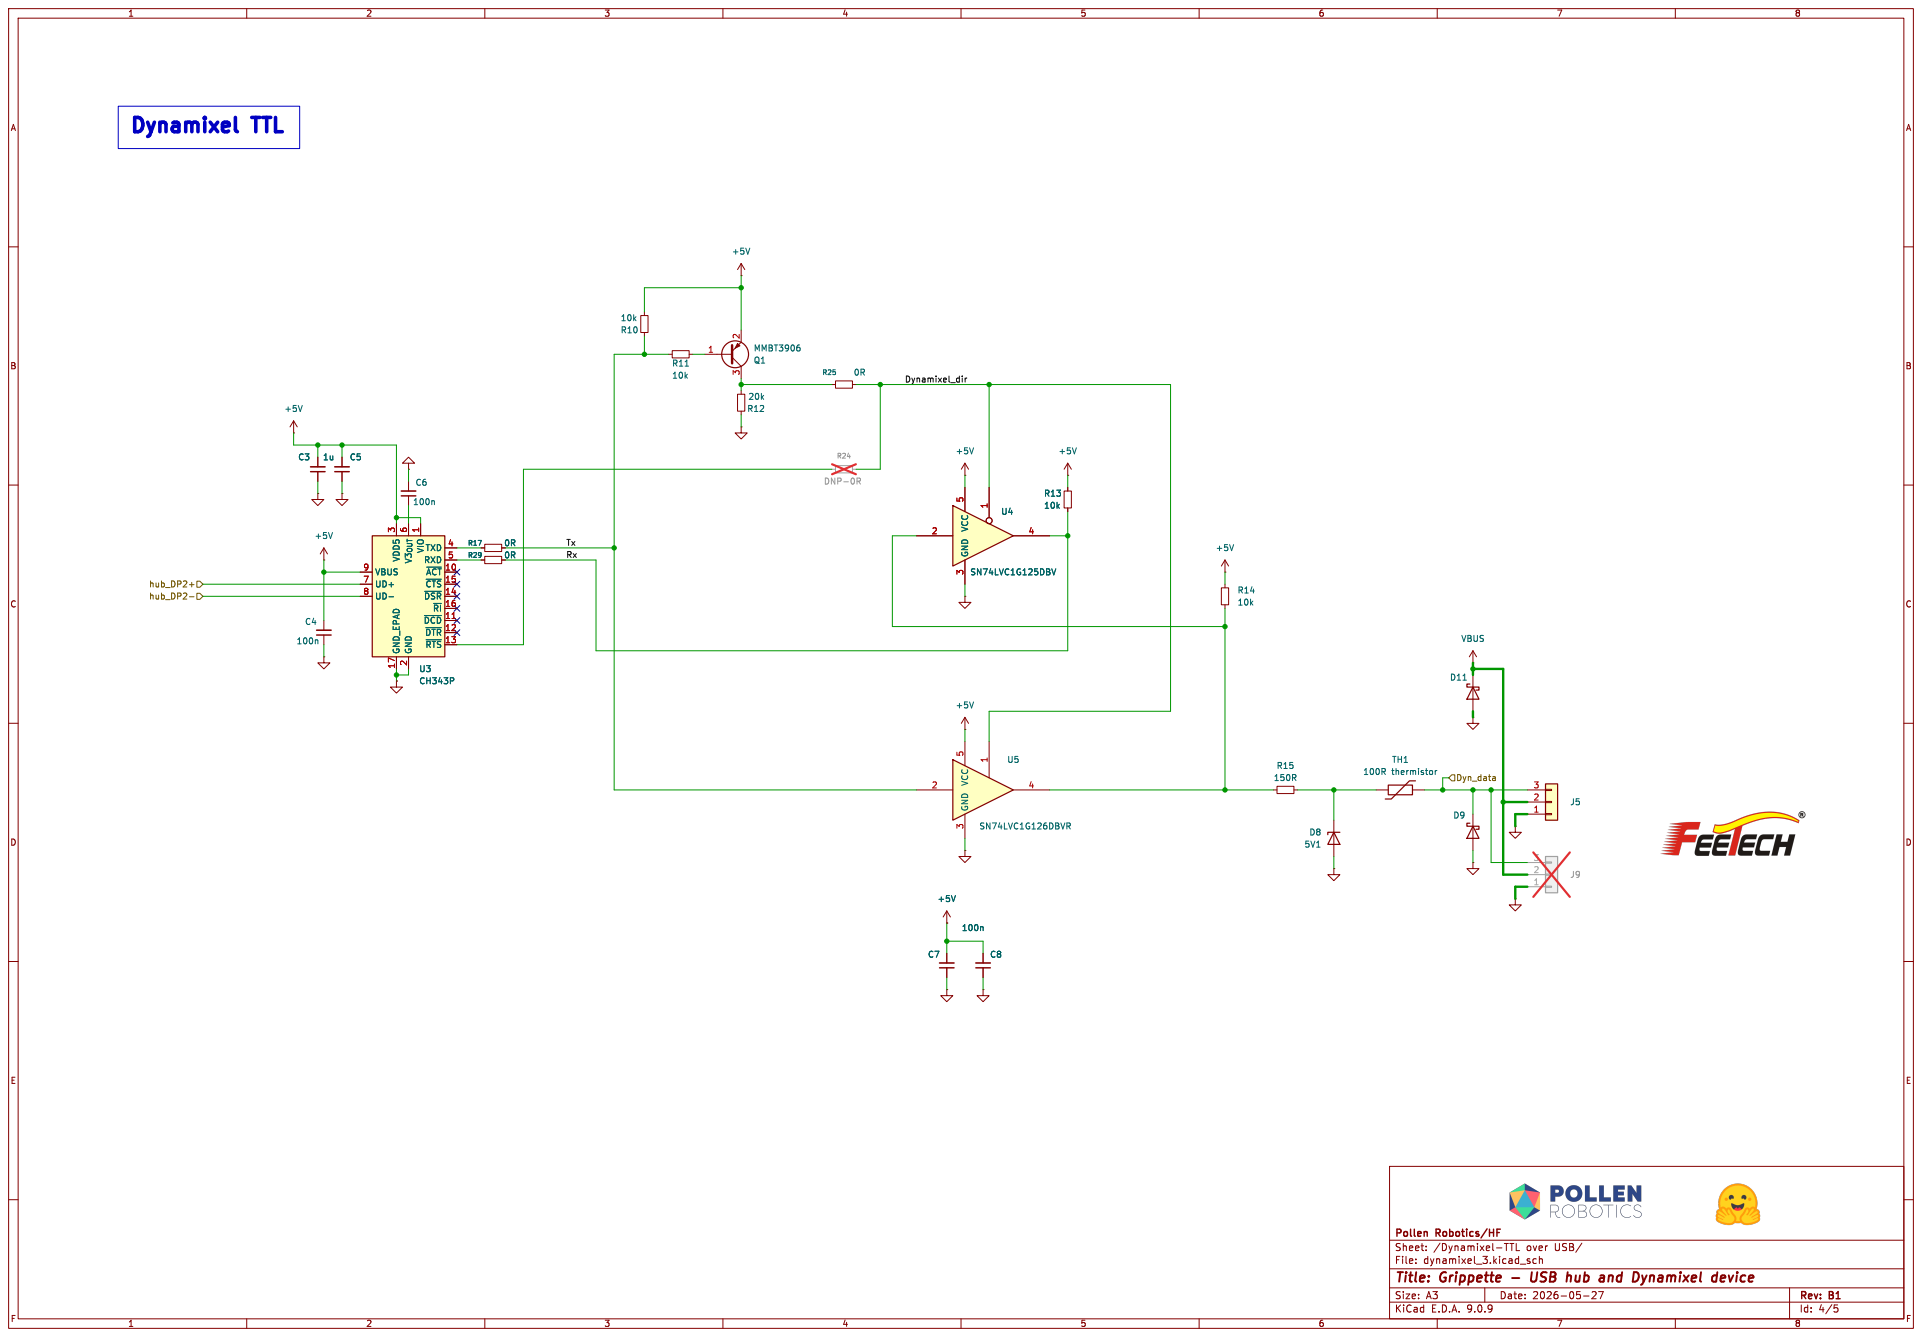
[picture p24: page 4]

1 TXD 4 RXD 5 ~{ACT} 10 ~{CTS} 15 ~{DSR} 14 ~{RI} 16 ~{DCD} 11 ~{DTR} 12 ~{RTS} 13 C3 1u C5 R17 0R

1 TXD 4 RXD 5 ~{ACT} 10 ~{CTS} 15 ~{DSR} 14 ~{RI} 16 ~{DCD} 11 ~{DTR} 12 ~{RTS} 13 U3 CH343P R15

Id: 4/5 Title: Grippette - USB hub and Dynamixel device

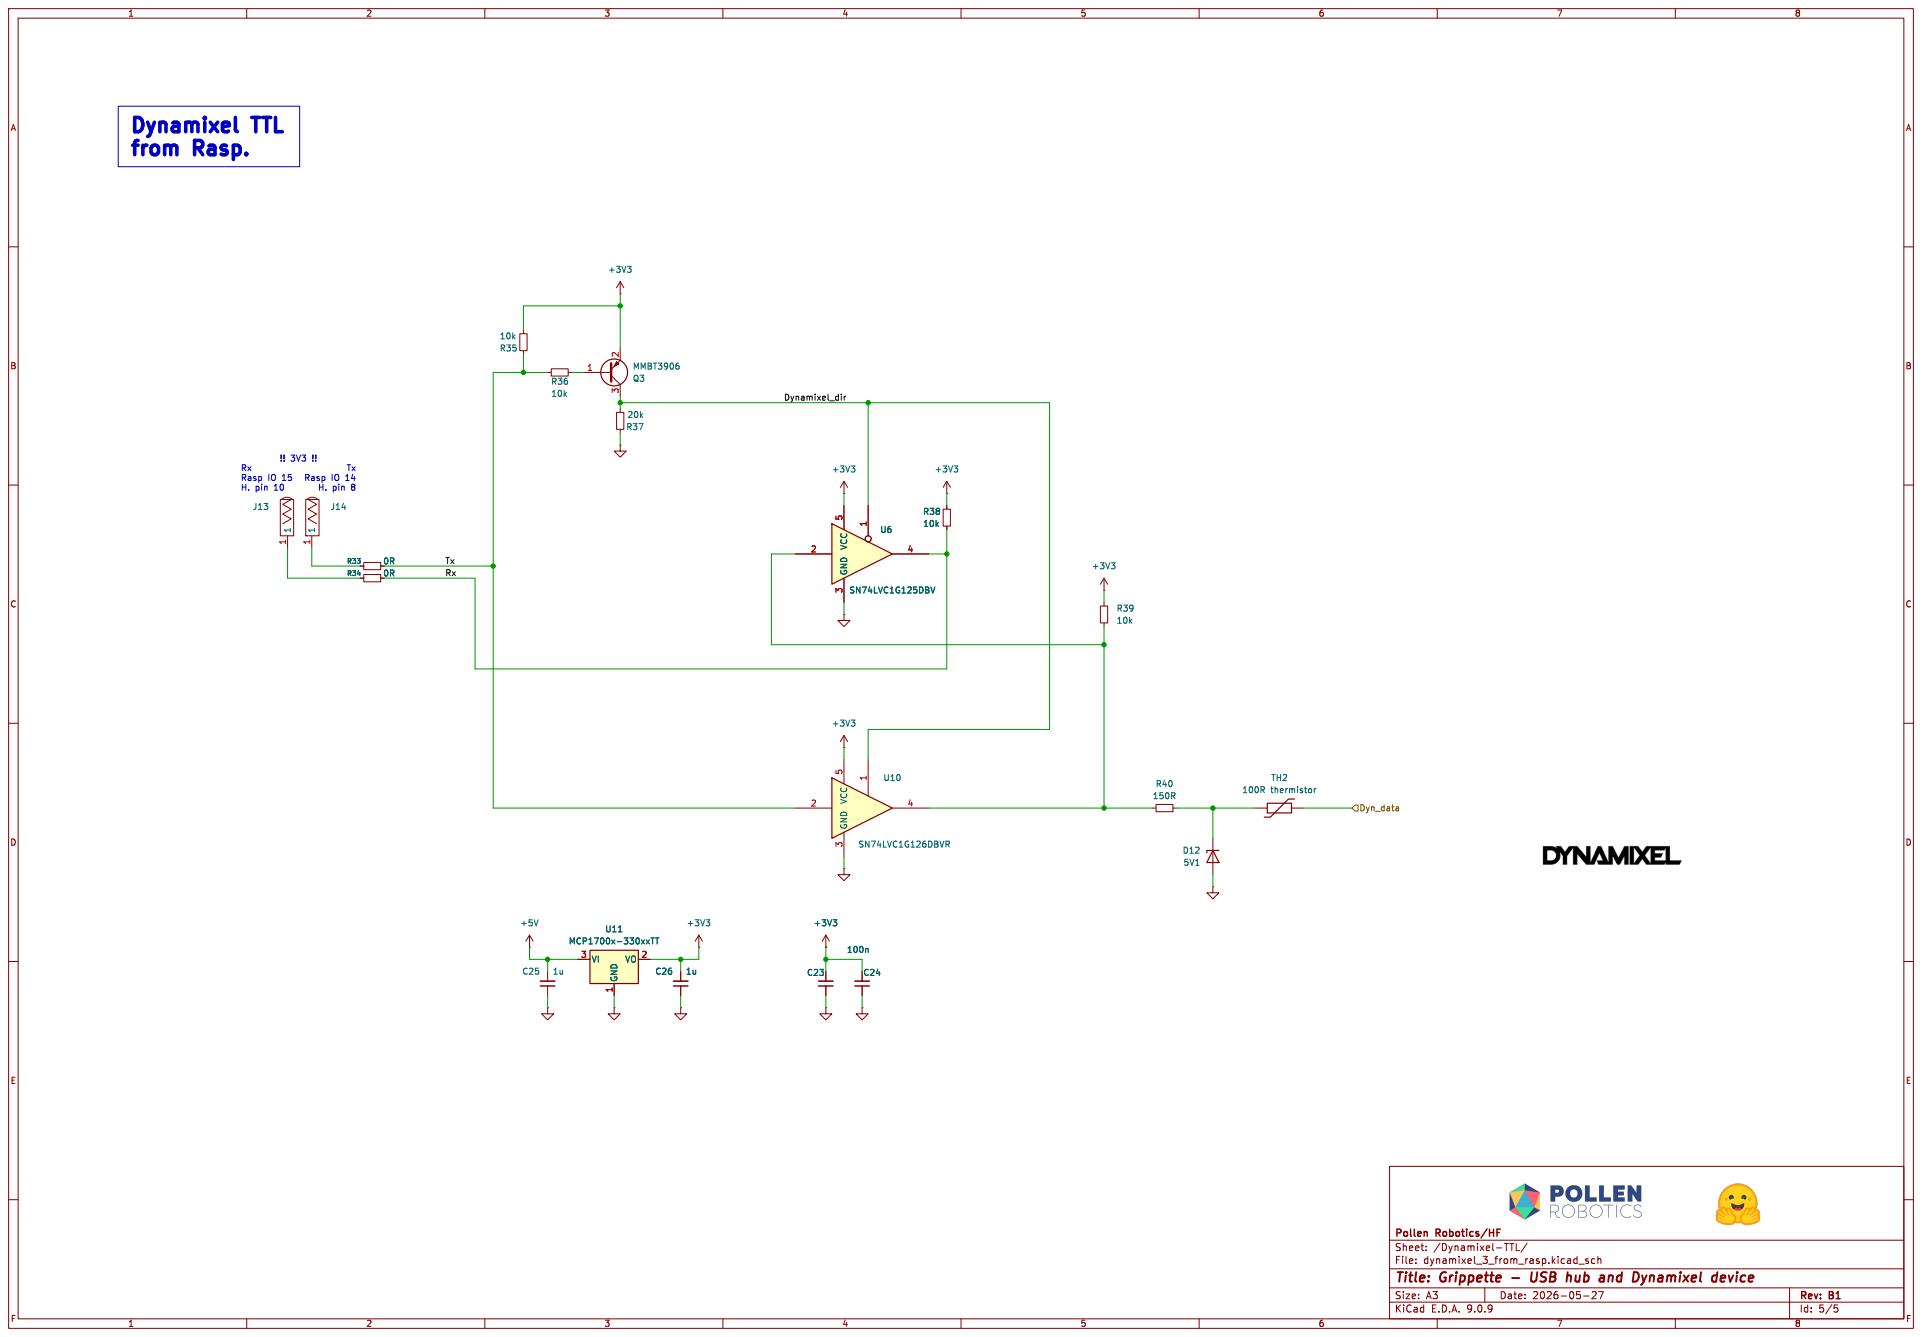
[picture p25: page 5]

Tx Rasp IO 14 H. pin 8

Id: 5/5 Title: Grippette - USB hub and Dynamixel device

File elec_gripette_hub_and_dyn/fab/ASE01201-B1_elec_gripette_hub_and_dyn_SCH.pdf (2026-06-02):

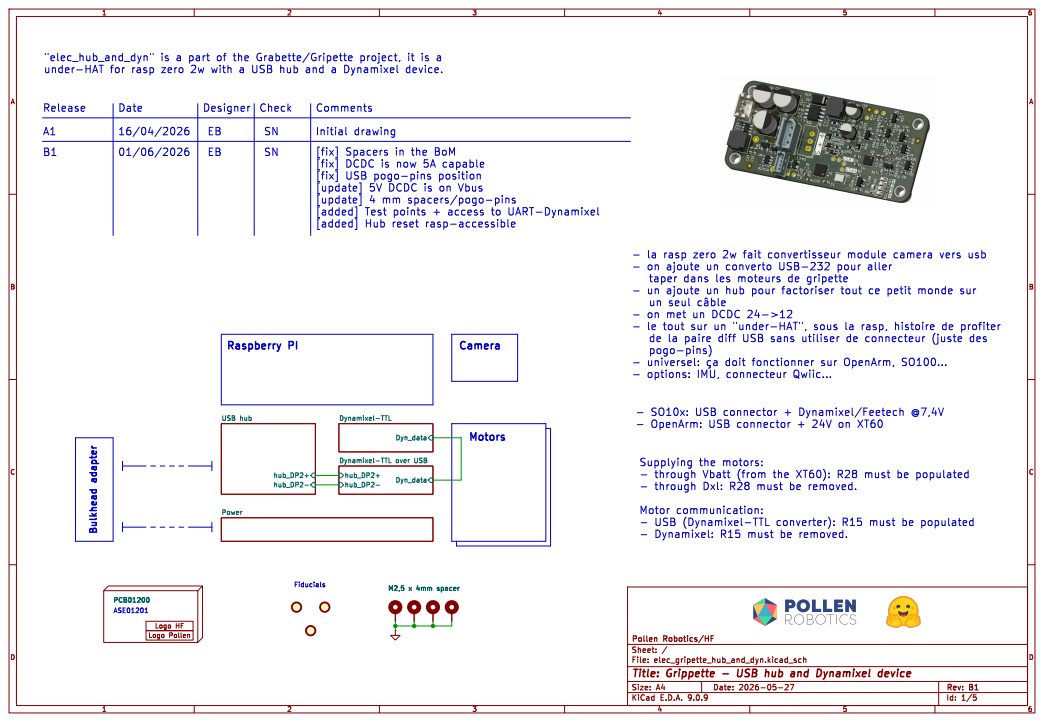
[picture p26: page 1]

taper dans les moteurs de gripette

- on met un DCDC 24->12
pogo-pins)

hub_DP2- hub_DP2+ USB hub Power Logo HF

Supplying the motors: - through Vbatt (from the XT60): R28 must be populated

- through Dxl: R28 must be removed.

- Dynamixel: R15 must be removed.

Id: 1/5 Title: Grippette - USB hub and Dynamixel device

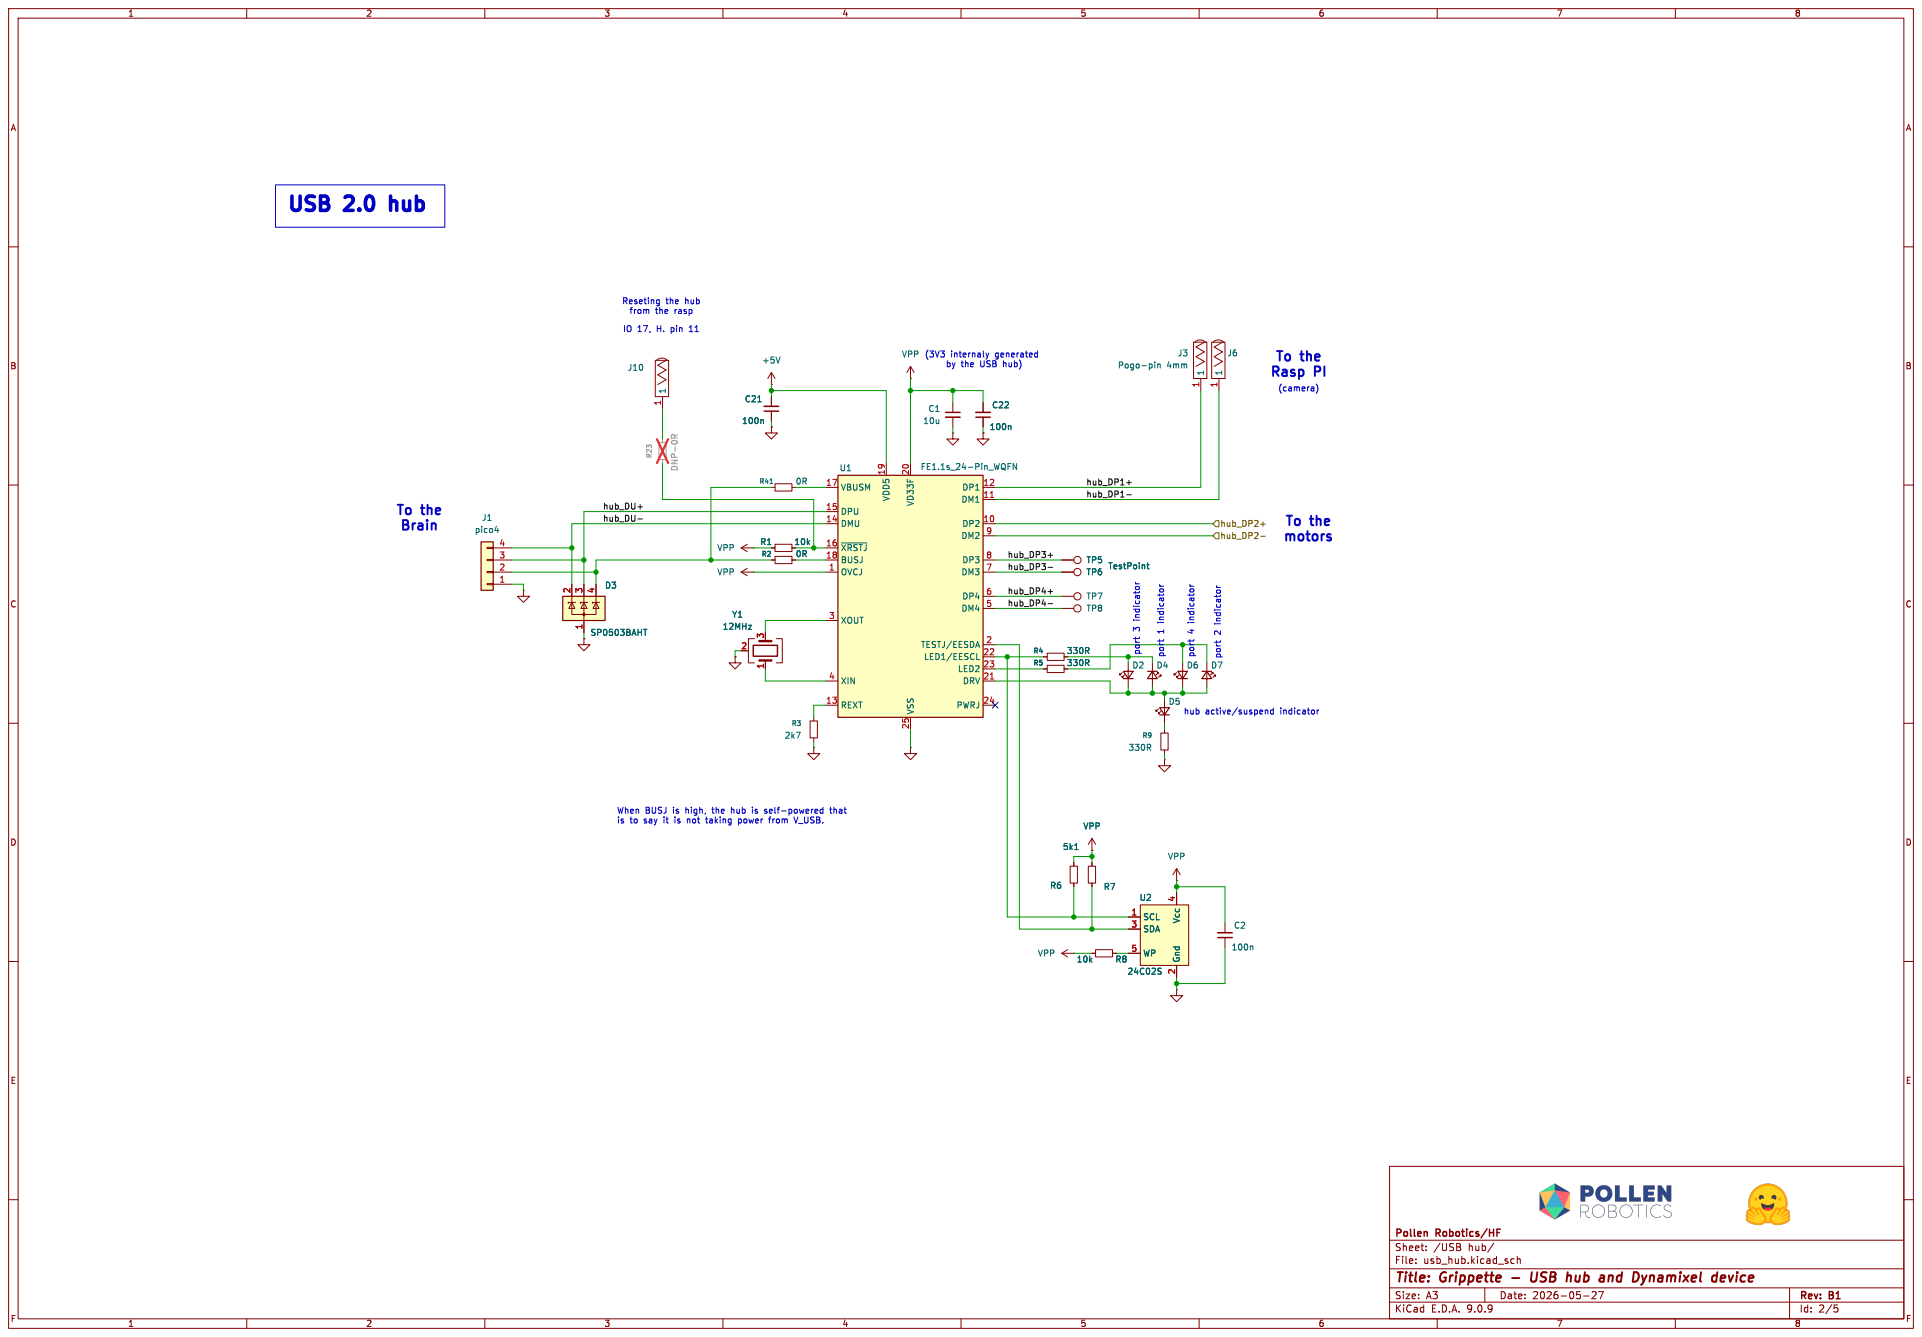
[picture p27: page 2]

Id: 2/5 Title: Grippette - USB hub and Dynamixel device

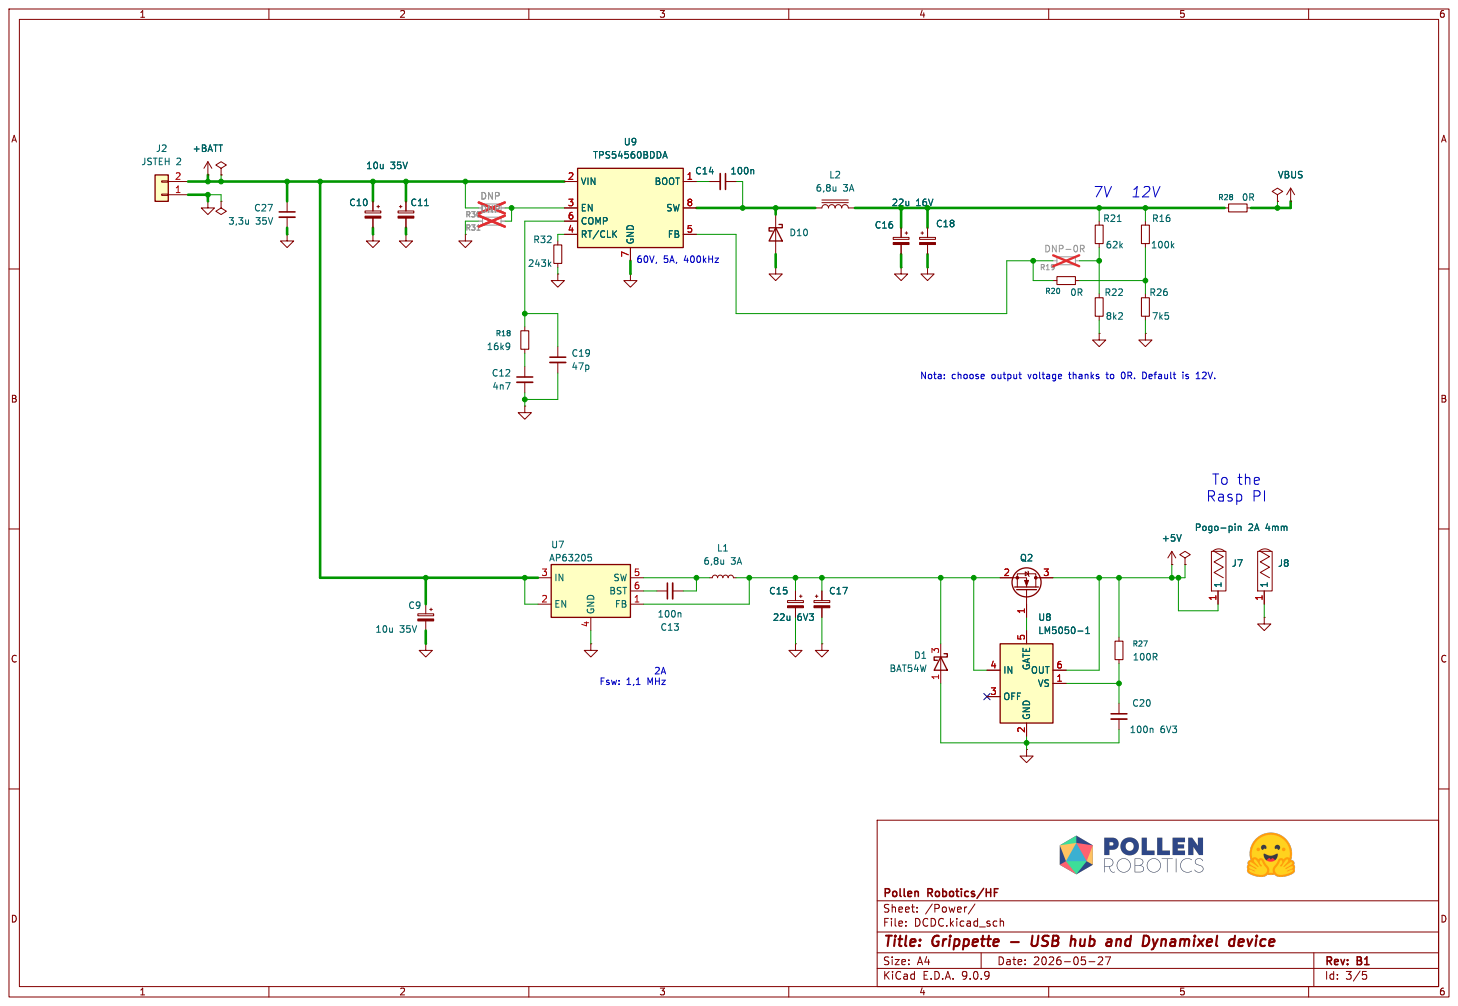
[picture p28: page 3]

Rasp PI Nota: choose output voltage thanks to 0R. Default is 12V. 7V

Id: 3/5 Title: Grippette - USB hub and Dynamixel device

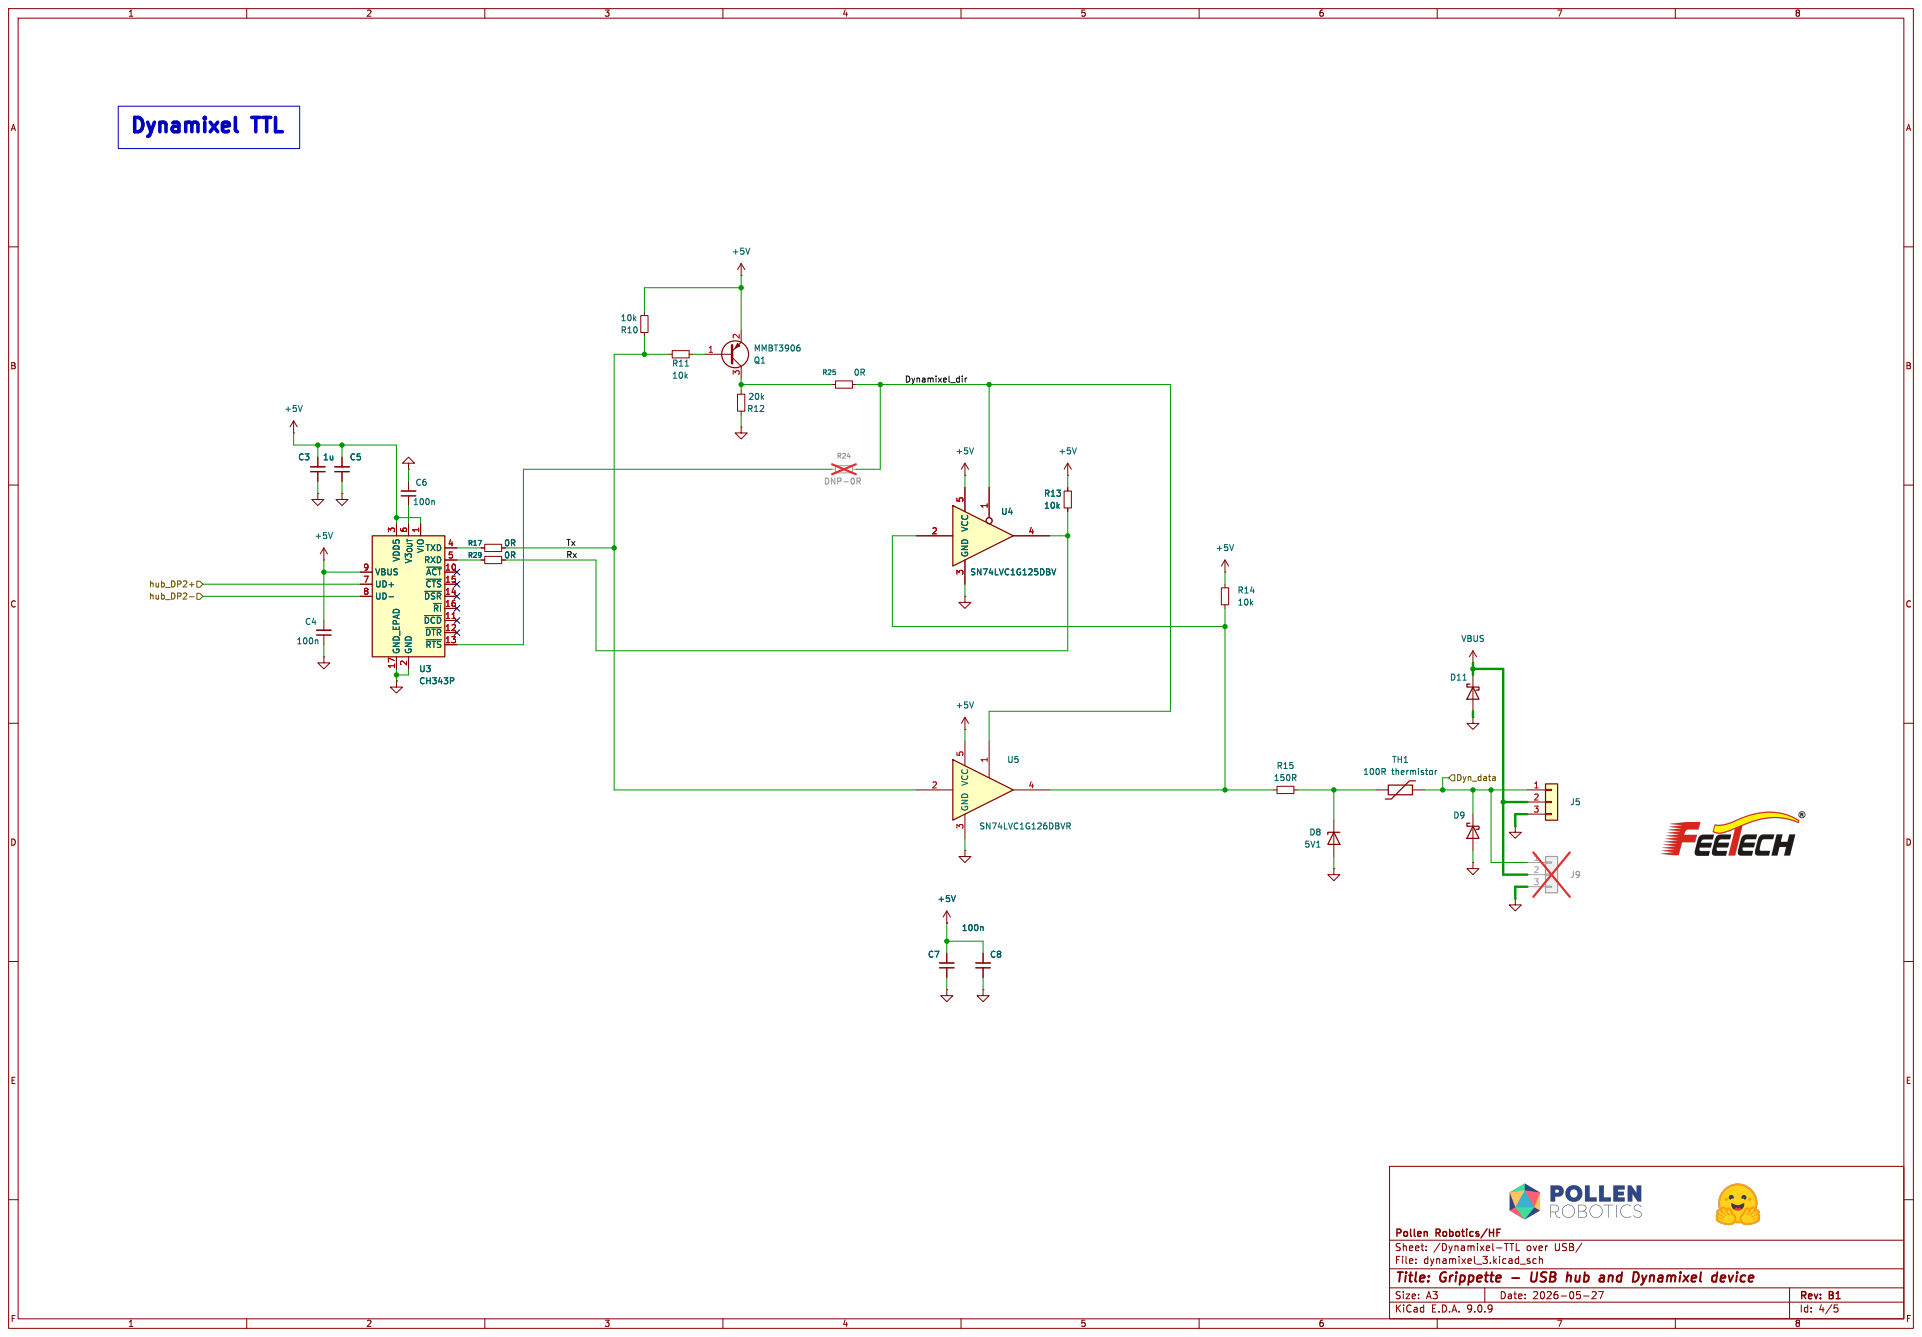
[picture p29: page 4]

1 TXD 4 RXD 5 ~{ACT} 10 ~{CTS} 15 ~{DSR} 14 ~{RI} 16 ~{DCD} 11 ~{DTR} 12 ~{RTS} 13 C3 1u C5 R17 0R

1 TXD 4 RXD 5 ~{ACT} 10 ~{CTS} 15 ~{DSR} 14 ~{RI} 16 ~{DCD} 11 ~{DTR} 12 ~{RTS} 13 U3 CH343P R15

Id: 4/5 Title: Grippette - USB hub and Dynamixel device


Tx Rasp IO 14 H. pin 8

Id: 5/5 Title: Grippette - USB hub and Dynamixel device

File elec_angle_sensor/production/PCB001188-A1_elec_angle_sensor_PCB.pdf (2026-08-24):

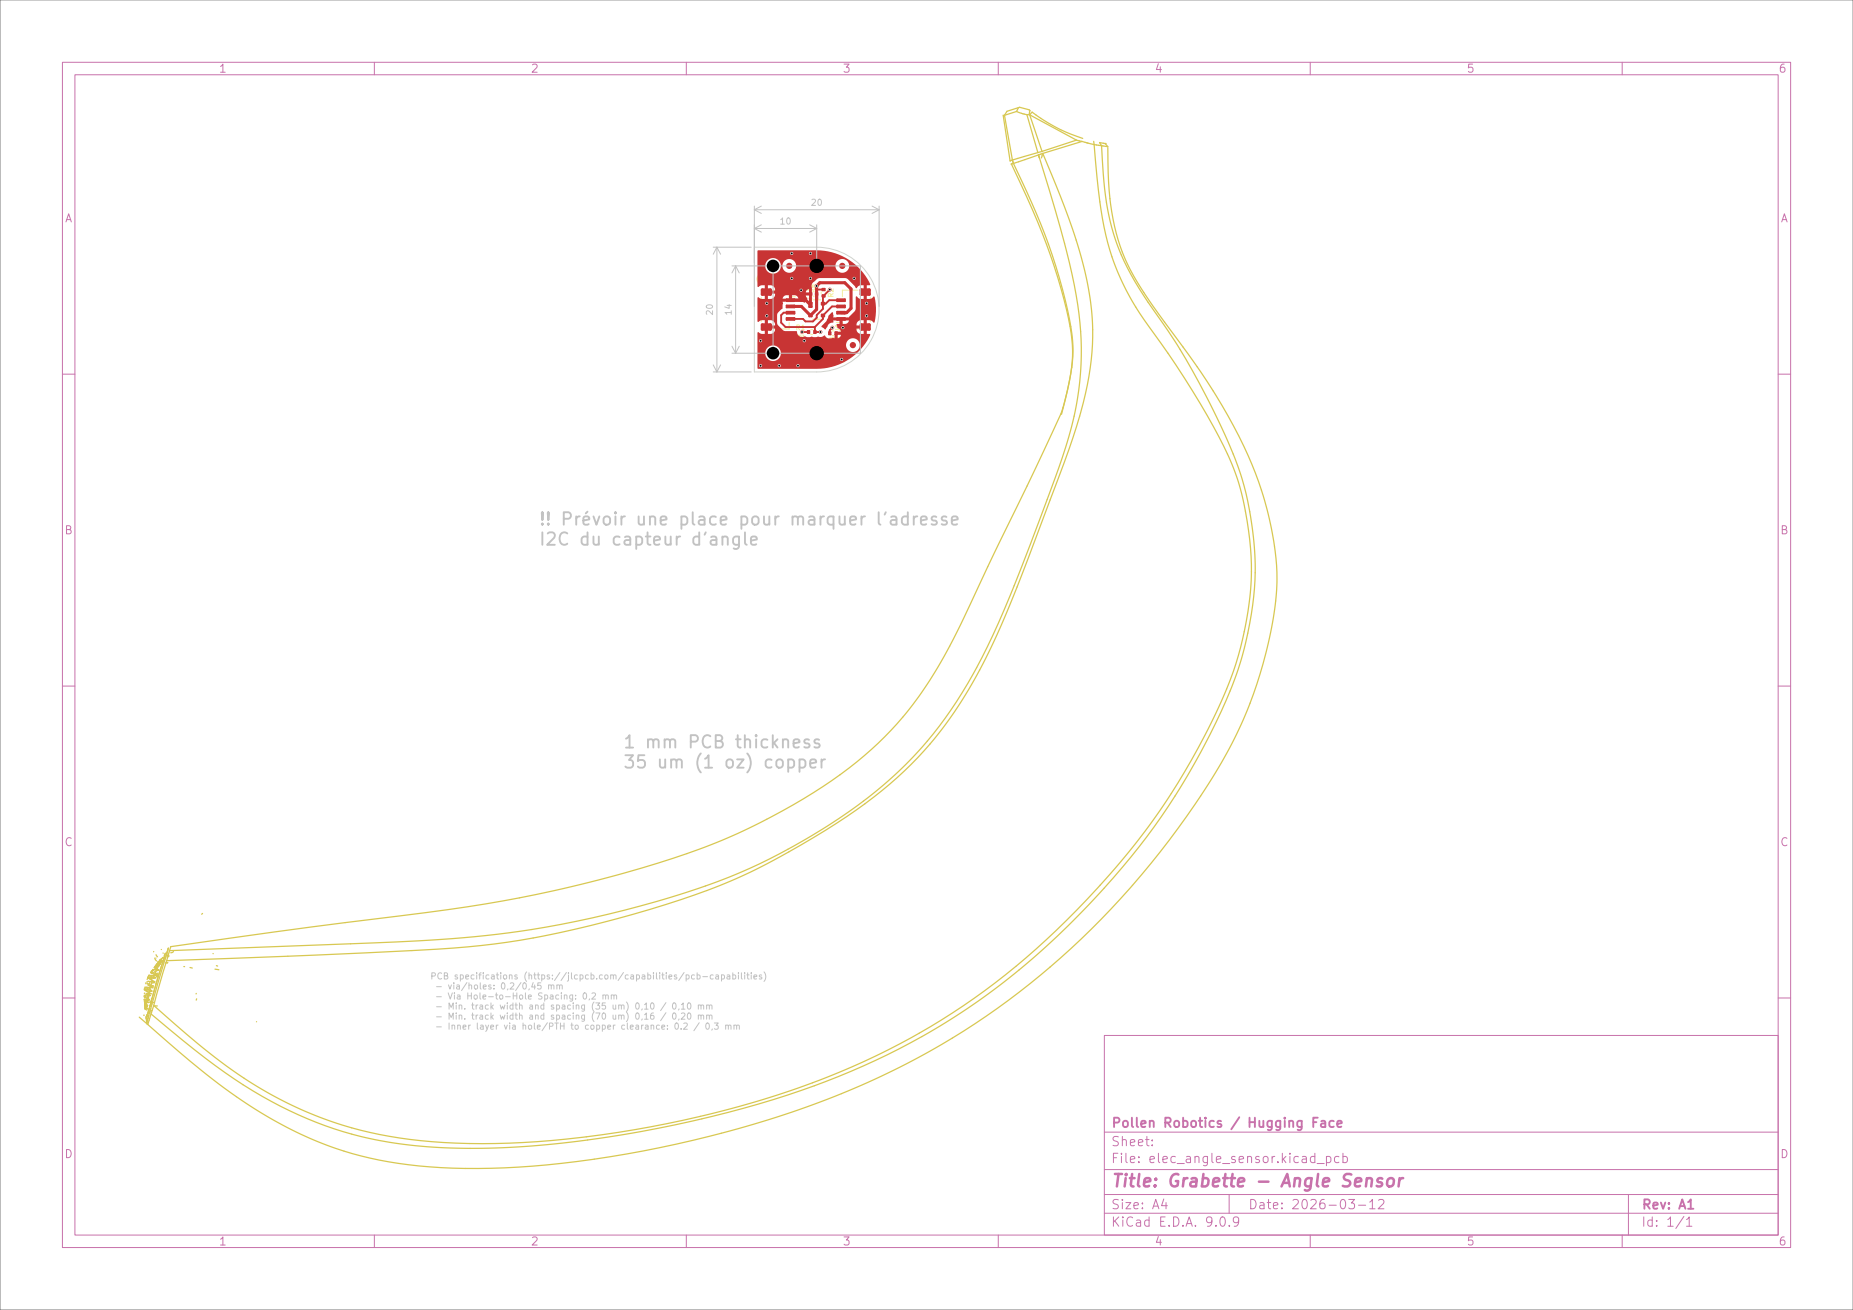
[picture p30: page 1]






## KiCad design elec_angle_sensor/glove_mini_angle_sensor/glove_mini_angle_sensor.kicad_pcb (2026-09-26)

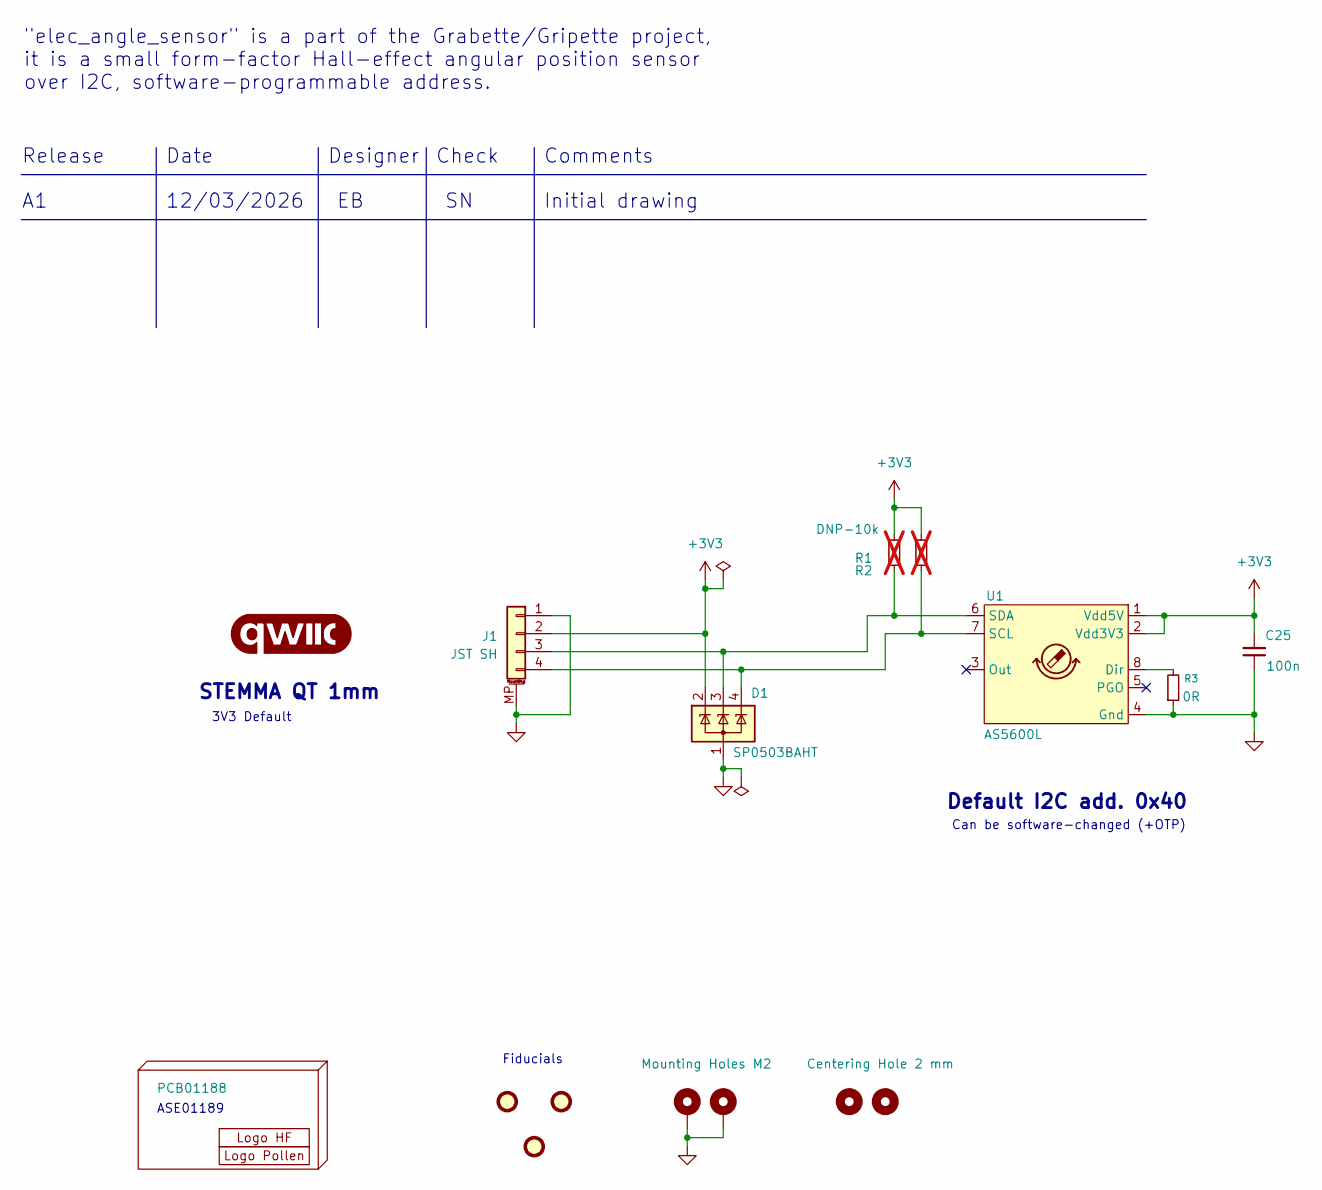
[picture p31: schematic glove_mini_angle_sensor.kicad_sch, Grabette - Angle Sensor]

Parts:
C25: 100n; C_0402_1005Metric; LCSC Part C307331
D1: SP0503BAHT; SOT-143; LCSC Part C41364459
FID1, FID2, FID3: DNP Fiducial; Fiducial_1mm_Mask2mm
G1: qwiic_Logo; Logo_qwiic_5mm
H1: PCB01188
H2: Logo HF 2025; Logo_HF_2025
H3: DNP Logo Pollen 2021; Logo_Pollen_2021_sq
H4, H5: Mounting Holes M2; MountingHole_2.2mm_M2_ISO7380_Pad_TopBottom
H6, H7: Centering Hole 2 mm; MountingHole_2.0mm
J1: JST SH; JST_SH_SM04B-SRSS-TB_1x04-1MP_P1.00mm_Horizontal; LCSC Part C160404
R1, R2: DNP-10k; R_0402_1005Metric; LCSC Part C25744; not fitted
R3: 0R; R_0402_1005Metric; LCSC Part C17168
U1: AS5600L; SOIC-8_3.9x4.9mm_P1.27mm; LCSC Part C2153666

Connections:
+3V3: C25.2, D1.2 (K), J1.2, R1.1, R2.1, U1.1 (Vdd5V), U1.2 (Vdd3V3)
GND: C25.1, D1.1 (A), H4.1 (1_1), H5.1 (1_1), J1.1, J1.MP (MountPin), R3.1, U1.4 (Gnd)
unnamed: D1.3 (K), J1.3, R1.2, U1.6 (SDA)
unnamed: D1.4 (K), J1.4, R2.2, U1.7 (SCL)
unnamed: R3.2, U1.8 (Dir)

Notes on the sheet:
Can be software-changed (+OTP)
Date
Check
Release
STEMMA QT 1mm
Fiducials
ASE01189
3V3 Default
Initial drawing
"elec_angle_sensor" is a part of the Grabette/Gripette project, it is a small form-factor Hall-effect angular position sensor over I2C, software-programmable address.
Designer
Default I2C add. 0x40
Comments
12/03/2026

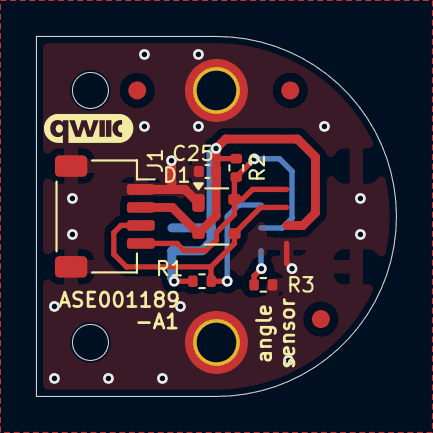
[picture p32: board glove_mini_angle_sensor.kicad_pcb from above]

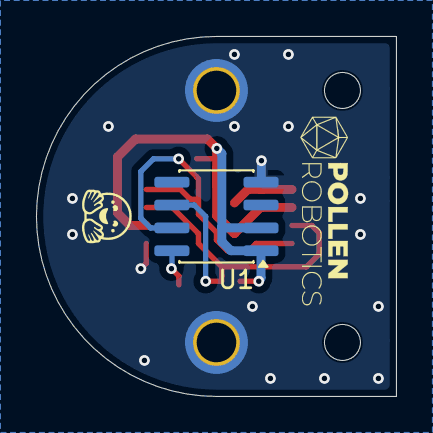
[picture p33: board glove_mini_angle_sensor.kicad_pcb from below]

Board: 2 copper layers, 20.0 x 20.0 mm, 17 parts (3 on the bottom side), 5 nets.

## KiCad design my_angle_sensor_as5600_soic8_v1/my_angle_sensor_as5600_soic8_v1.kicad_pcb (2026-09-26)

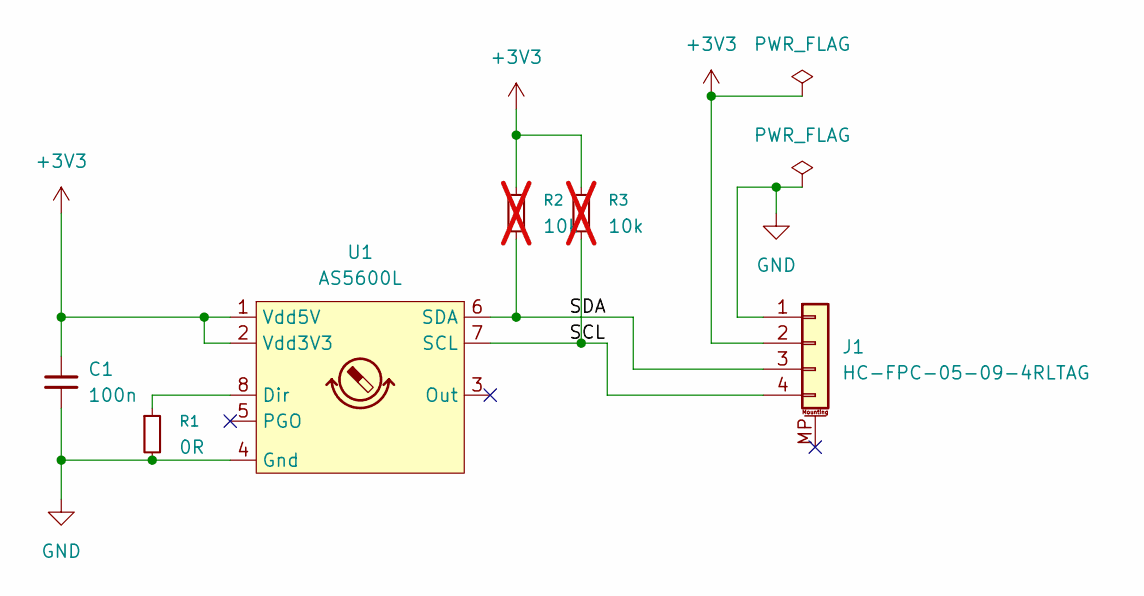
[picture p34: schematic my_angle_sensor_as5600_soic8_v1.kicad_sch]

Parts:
C1: 100n; C_0402_1005Metric
J1: HC-FPC-05-09-4RLTAG
R1: 0R; R_0402_1005Metric
R2, R3: 10k; R_0402_1005Metric; not fitted
U1: AS5600L; SOIC-8_3.9x4.9mm_P1.27mm; LCSC Part C2153666

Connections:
+3V3: C1.1, J1.2, R2.1, R3.1, U1.1 (Vdd5V), U1.2 (Vdd3V3)
/SCL: J1.4, R3.2, U1.7 (SCL)
/SDA: J1.3, R2.2, U1.6 (SDA)
GND: C1.2, J1.1, R1.2, U1.4 (Gnd)
unnamed: R1.1, U1.8 (Dir)

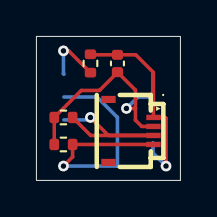
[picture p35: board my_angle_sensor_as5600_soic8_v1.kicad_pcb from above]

Board: 2 copper layers, 8.0 x 8.0 mm, 6 parts (1 on the bottom side), 5 nets.

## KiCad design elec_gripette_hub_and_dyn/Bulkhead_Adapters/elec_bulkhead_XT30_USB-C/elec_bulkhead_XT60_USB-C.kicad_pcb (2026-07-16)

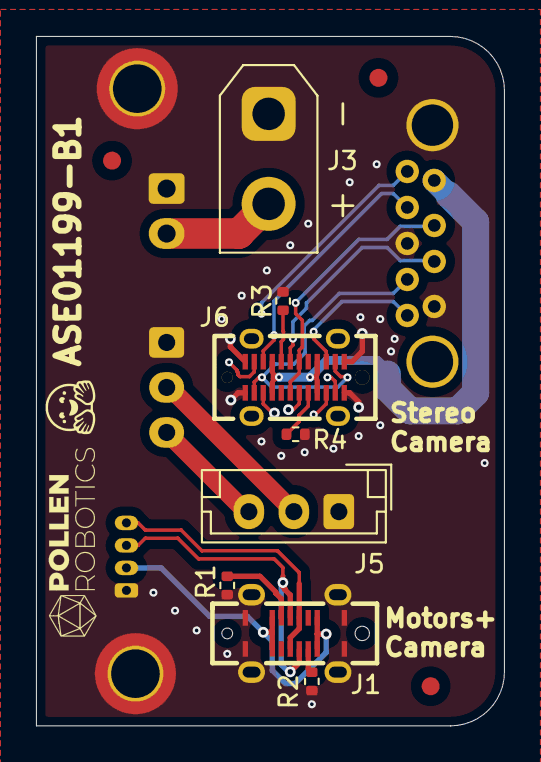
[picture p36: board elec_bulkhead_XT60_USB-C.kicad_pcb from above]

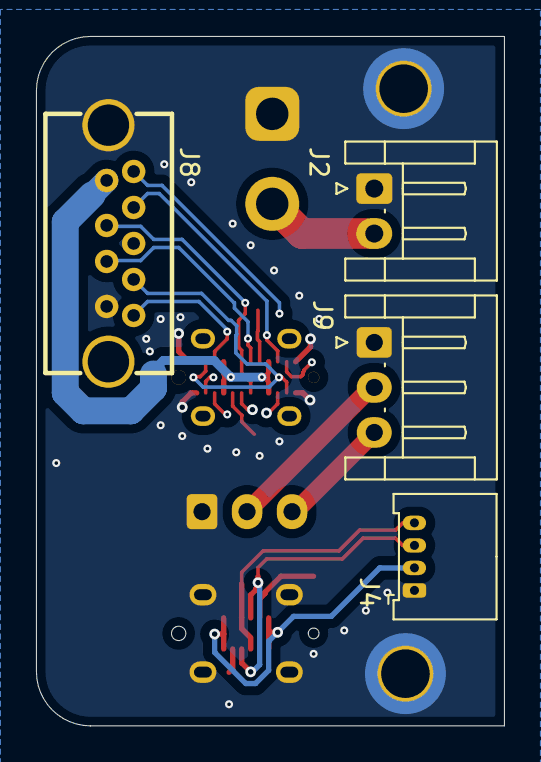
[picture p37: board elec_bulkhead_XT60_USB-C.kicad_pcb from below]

Board: 4 copper layers, 26.0 x 38.3 mm, 19 parts (4 on the bottom side), 18 nets.

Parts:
FID1, FID2, FID3: DNP Fiducial; Fiducial_1mm_Mask2mm
H2: Logo HF 2025; Logo_HF_2025
H3: DNP Logo Pollen 2021; Logo_Pollen_2021_sq
H4, H5: Mounting Hole M2,5; MountingHole_2.7mm_M2.5_ISO14580_Pad_TopBottom
J1: USB-C Rec. Vert.; USB-C_16p_vert_Shou-Han_TYPE-C 16P LTH6.8 - C5187468
J2: JST EH 2; JST_EH_S2B-EH_1x02_P2.50mm_Horizontal
J3: XT30; AMASS_XT30UPB-M_1x02_P5.0mm_Vertical
J4: pico4; Molex_PicoBlade_53048-0410_1x04_P1.25mm_Horizontal
J5: DNP - Dynamixel-3; JST_EH_B3B-EH-A_1x03_P2.50mm_Vertical
J6: USB_C_Receptacle; USB-C_TYPE-C-24PLT-H10.5-1
J8: USB3_A; USB-A-TH_MOLEX_484080003
J9: DNP - Dynamixel-3; JST_EH_S3B-EH_1x03_P2.50mm_Horizontal
R1, R2, R3, R4: 5k1; R_0402_1005Metric

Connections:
+BATT: J2.2, J3.2
/D+: J6.A6 (D+), J6.B6 (D+), J8.3 (D+)
/D-: J6.A7 (D-), J6.B7 (D-), J8.2 (D-)
/DM+: J1.A6 (D+), J1.B6 (D+), J4.3
/DM-: J1.A7 (D-), J1.B7 (D-), J4.4
/SSRx+: J6.A11 (RX2+), J6.B11 (RX1+), J8.6 (SSRX+)
/SSRx-: J6.A10 (RX2-), J6.B10 (RX1-), J8.5 (SSRX-)
/SSTx+: J6.A2 (TX1+), J6.B2 (TX2+), J8.9 (SSTX+)
/SSTx-: J6.A3 (TX1-), J6.B3 (TX2-), J8.8 (SSTX-)
GND: H4.1, H5.1, J1.A1 (GND), J1.A12 (GND), J1.B1 (GND), J1.B12 (GND), J1.S1 (SHIELD), J2.1, J3.1, J4.1, J5.1, J6.A1 (GND), J6.A12 (GND), J6.B1 (GND), J6.B12 (GND), J8.4 (GND), J8.7 (DRAIN), J8.10 (SHIELD), J9.1, R1.2, R2.2, R3.2, R4.2
unnamed: J1.A5 (CC1), R1.1
unnamed: J1.B5 (CC2), R2.1
unnamed: J1.A4 (VBUS), J1.A9 (VBUS), J1.B4 (VBUS), J1.B9 (VBUS), J4.2
unnamed: J5.2, J9.2
unnamed: J5.3, J9.3
unnamed: J6.A5 (CC1), R3.1
unnamed: J6.B5 (CC2), R4.1
unnamed: J6.A4 (VBUS), J6.A9 (VBUS), J6.B4 (VBUS), J6.B9 (VBUS), J8.1 (VBUS)

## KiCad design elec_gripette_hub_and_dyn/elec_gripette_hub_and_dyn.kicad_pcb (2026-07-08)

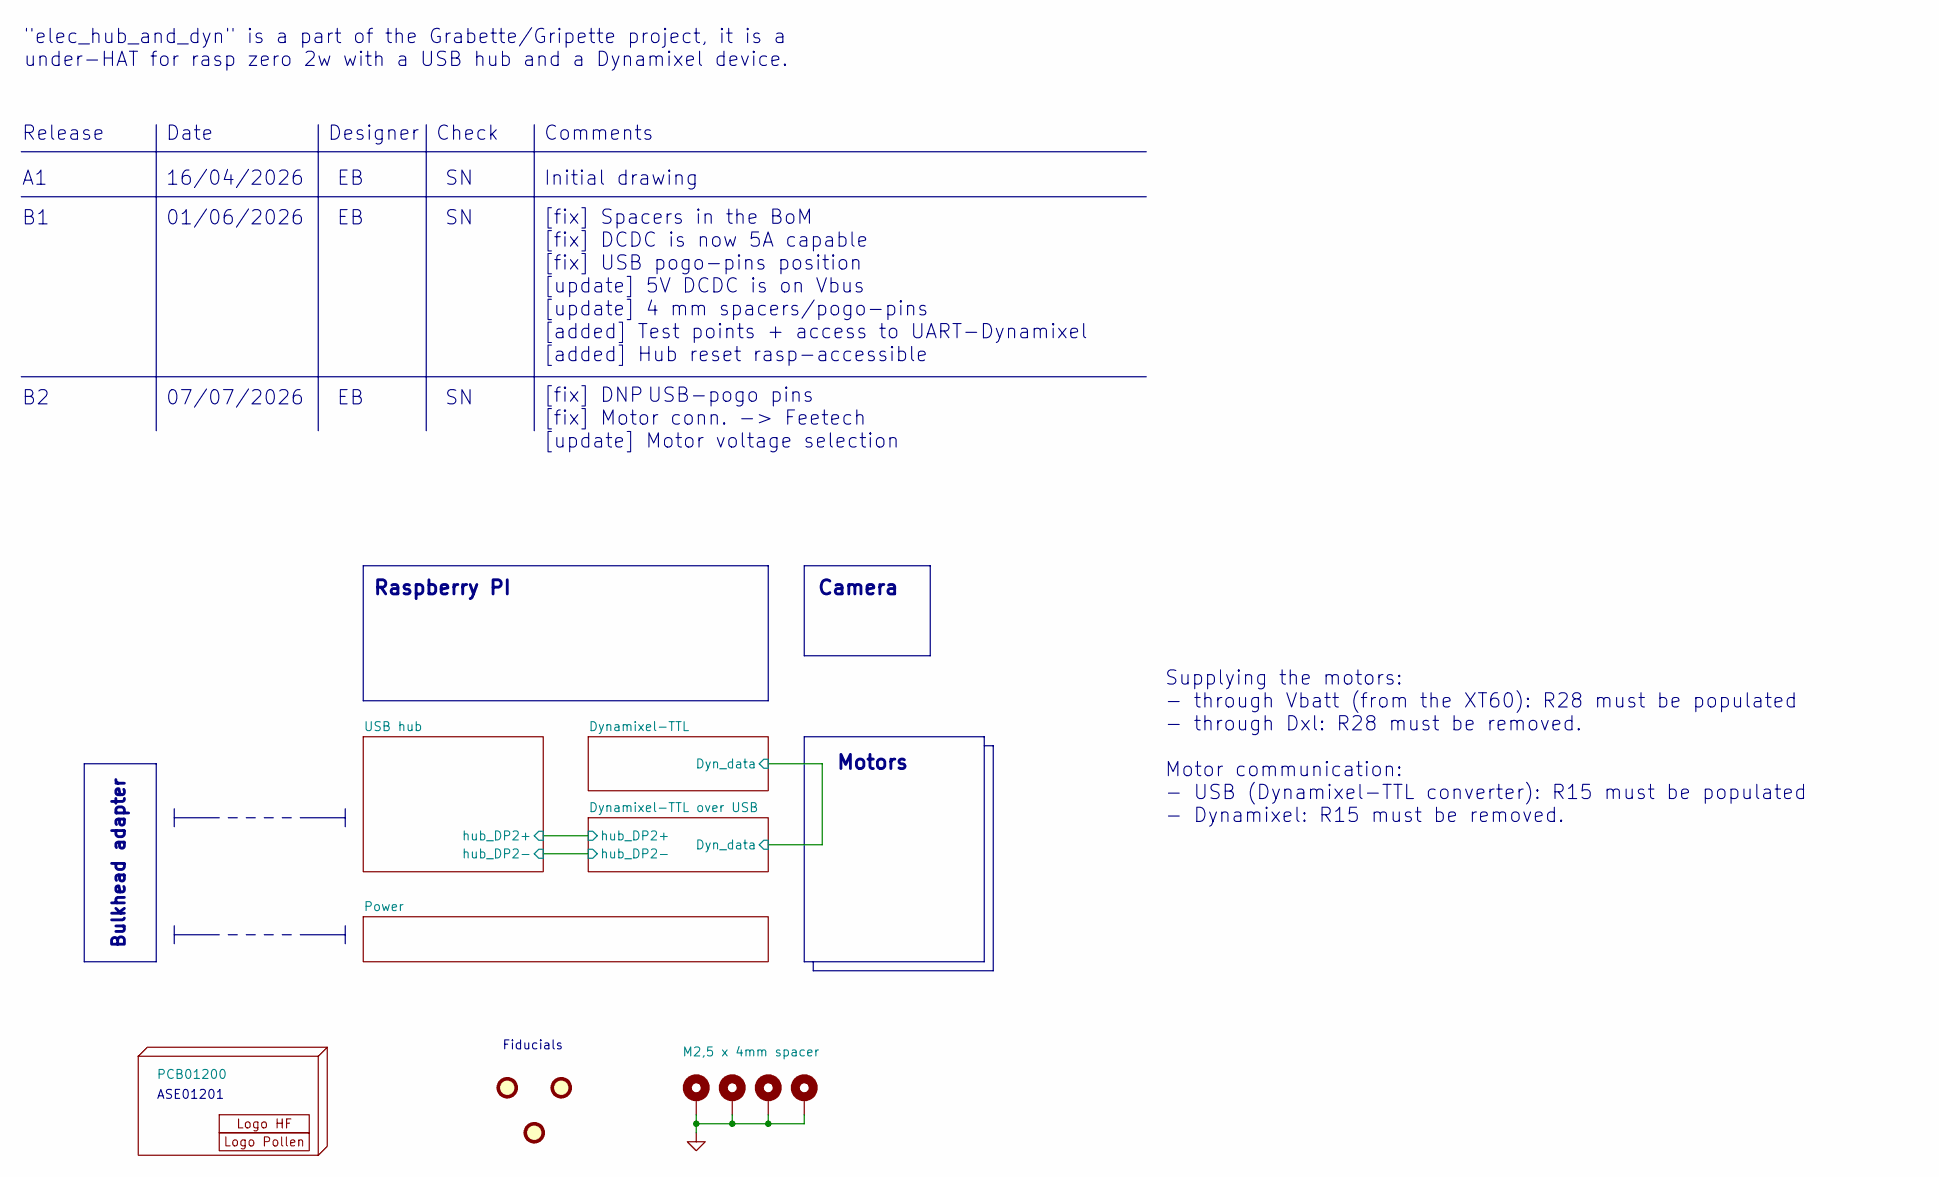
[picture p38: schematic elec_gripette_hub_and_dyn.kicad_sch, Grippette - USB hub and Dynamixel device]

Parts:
FID1, FID2, FID3: DNP Fiducial; Fiducial_1mm_Mask2mm
H1: PCB01200
H2: Logo HF 2025; Logo_HF_2025
H3: DNP Logo Pollen 2021; Logo_Pollen_2021_sq
H4, H5, H6, H7: M2,5 x 4mm spacer; SMD_BD5.6-D4.1_spacer; LCSC Part C2916324

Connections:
GND: H4.1, H5.1, H6.1, H7.1; also elsewhere on the board

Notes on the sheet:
Date
[fix] Spacers in the BoM [fix] DCDC is now 5A capable [fix] USB pogo-pins position [update] 5V DCDC is on Vbus [update] 4 mm spacers/pogo-pins [added] Test points + access to UART-Dynamixel [added] Hub reset rasp-accessible
Check
Release
Fiducials
ASE01201
Motors
Supplying the motors: - through Vbatt (from the XT60): R28 must be populated - through Dxl: R28 must be removed. Motor communication: - USB (Dynamixel-TTL converter): R15 must be populated - Dynamixel: R15 must be removed.
Raspberry PI
Camera
Initial drawing
"elec_hub_and_dyn" is a part of the Grabette/Gripette project, it is a under-HAT for rasp zero 2w with a USB hub and a Dynamixel device.
Designer
[fix] DNP USB-pogo pins [fix] Motor conn. -> Feetech [update] Motor voltage selection
Bulkhead adapter
07/07/2026
01/06/2026
Comments
16/04/2026

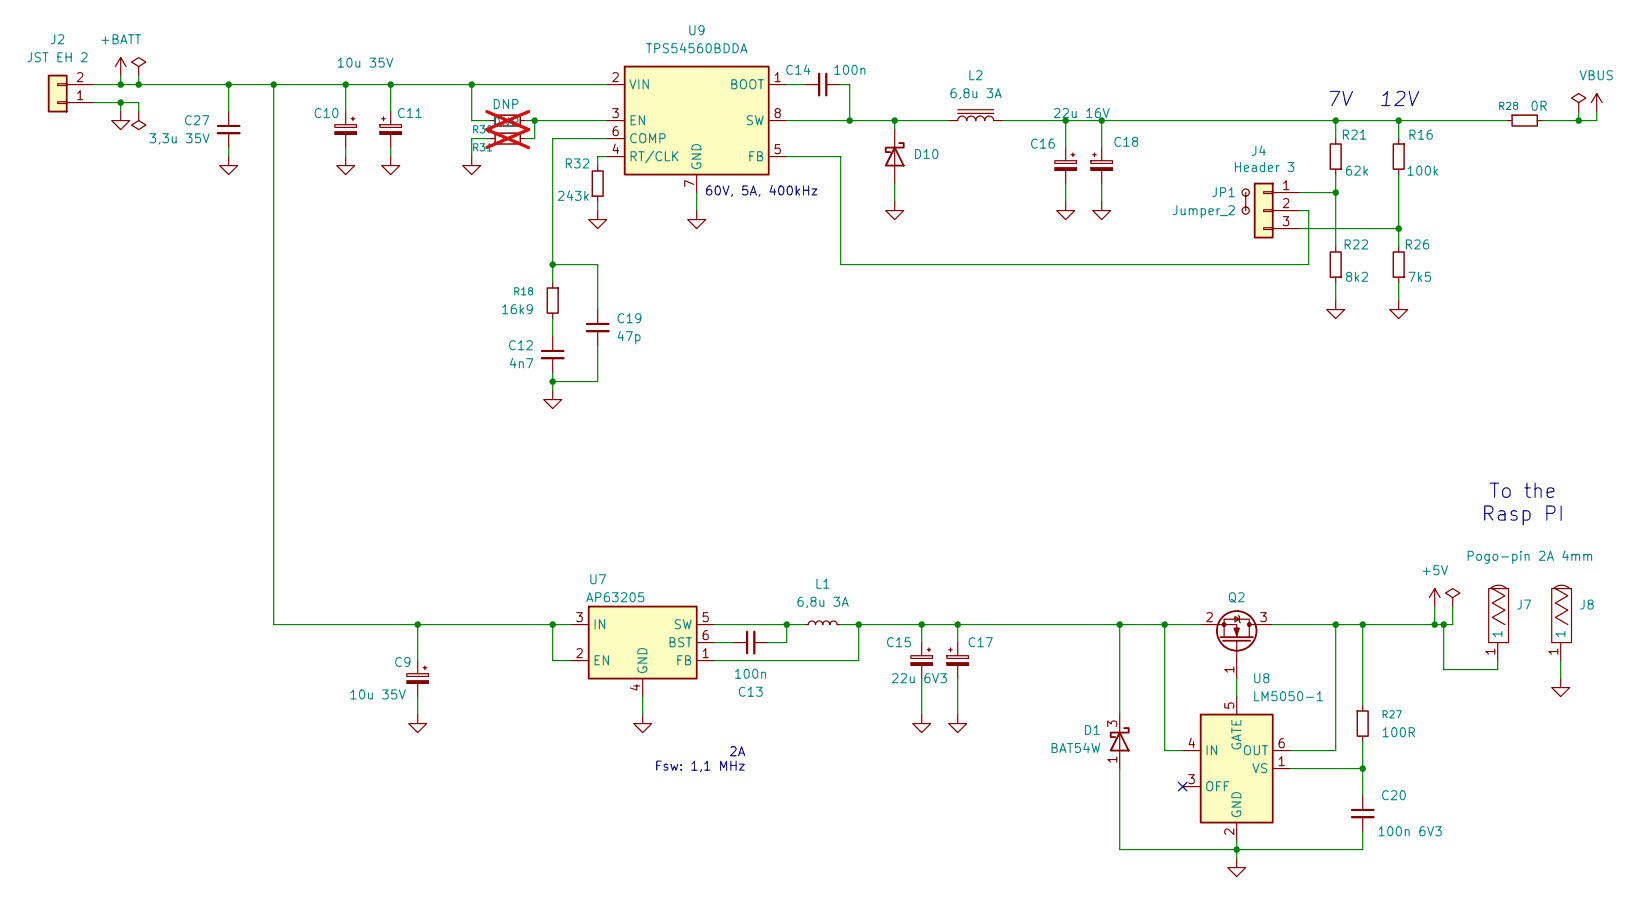
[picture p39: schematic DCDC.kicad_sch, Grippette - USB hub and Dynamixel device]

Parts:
C9, C10, C11: 10u 35V; CP_Elec_6.3x7.7; LCSC Part C72488
C12: 4n7; C_0402_1005Metric; LCSC Part C1518204
C13, C14: 100n; C_0402_1005Metric; LCSC Part C307331
C15, C17: 22u 6V3; C_0603_1608Metric; LCSC Part C84419
C16, C18: 22u 16V; CP_Elec_4x5.4; LCSC Part C72502
C19: 47p; C_0402_1005Metric; LCSC Part C1567
C20: 100n 6V3; C_0402_1005Metric; LCSC Part C1525
C27: 3,3u 35V; C_0805_2012Metric; LCSC Part C361184
D1: BAT54W; SOT-323_SC-70; LCSC Part C78606
D10: D_Schottky 3A; D_SMA; LCSC Part C8678
J2: JST EH 2; JST_EH_B2B-EH-A_1x02_P2.50mm_Vertical; LCSC Part C160262
J4: Header 3; PinHeader_1x03_P1.27mm_Vertical; LCSC Part C7470079
J7, J8: Pogo-pin 2A 4mm; CONN-TH_YZ08415060P-02_pogo; LCSC Part C7471674
JP1: Jumper_2; LCSC Part C150949
L1, L2: 6,8u 3A; L_Bourns_SRN6045TA; LCSC Part C57254
Q2: SI2312CDS-T1-GE3; TSOT-23; LCSC Part C142518
R16: 100k; R_0402_1005Metric; LCSC Part C2906883
R18: 16k9; R_0402_1005Metric; LCSC Part C25858
R21: 62k; R_0402_1005Metric; LCSC Part C2909375
R22: 8k2; R_0402_1005Metric; LCSC Part C25924
R26: 7k5; R_0402_1005Metric; LCSC Part C25918
R27: 100R; R_0402_1005Metric; LCSC Part C2906860
R28: 0R; R_0603_1608Metric; LCSC Part C21189
R30, R31: DNP; R_0402_1005Metric; not fitted
R32: 243k; R_0402_1005Metric; LCSC Part C43249
U7: AP63205; TSOT-23-6; LCSC Part C2071056
U8: LM5050-1; TSOT-23-6; LCSC Part C473393
U9: TPS54560BDDA; Texas_R-PDSO-G8_EP2.95x4.9mm_Mask2.4x3.1mm_ThermalVias; LCSC Part C1850354

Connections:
+5V: J7.1, Q2.3 (D), R27.1, U8.6 (OUT); also elsewhere on the board
+BATT: C9.1, C10.1, C11.1, C27.1, J2.2, R30.1, U7.2 (EN), U7.3 (IN), U9.2 (VIN)
GND: C9.2, C10.2, C11.2, C12.2, C15.2, C16.2, C17.2, C18.2, C19.2, C20.2, C27.2, D1.1 (A), D10.2 (A), J2.1, J8.1, R22.1, R26.1, R31.1, R32.1, U7.4 (GND), U8.2 (GND), U9.7 (GND), U9.9 (GND); also elsewhere on the board
unnamed: C12.1, R18.2
unnamed: C16.1, C18.1, L2.1, R16.1, R21.2, R28.1
unnamed: C15.1, C17.1, D1.3 (K), L1.1, Q2.2 (S), U7.1 (FB), U8.4 (IN)
unnamed: C14.1, D10.1 (K), L2.2, U9.8 (SW)
unnamed: J4.1, R21.1, R22.2
unnamed: J4.2, U9.5 (FB)
unnamed: J4.3, R16.2, R26.2
unnamed: Q2.1 (G), U8.5 (GATE)
unnamed: C13.1, U7.6 (BST)
unnamed: C13.2, L1.2, U7.5 (SW)
unnamed: C20.1, R27.2, U8.1 (VS)
unnamed: C14.2, U9.1 (BOOT)
unnamed: C19.1, R18.1, U9.6 (COMP)
unnamed: R30.2, R31.2, U9.3 (EN)
unnamed: R32.2, U9.4 (RT/CLK)
VBUS: R28.2; also elsewhere on the board

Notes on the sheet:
60V, 5A, 400kHz
2A Fsw: 1,1 MHz
To the Rasp PI
12V

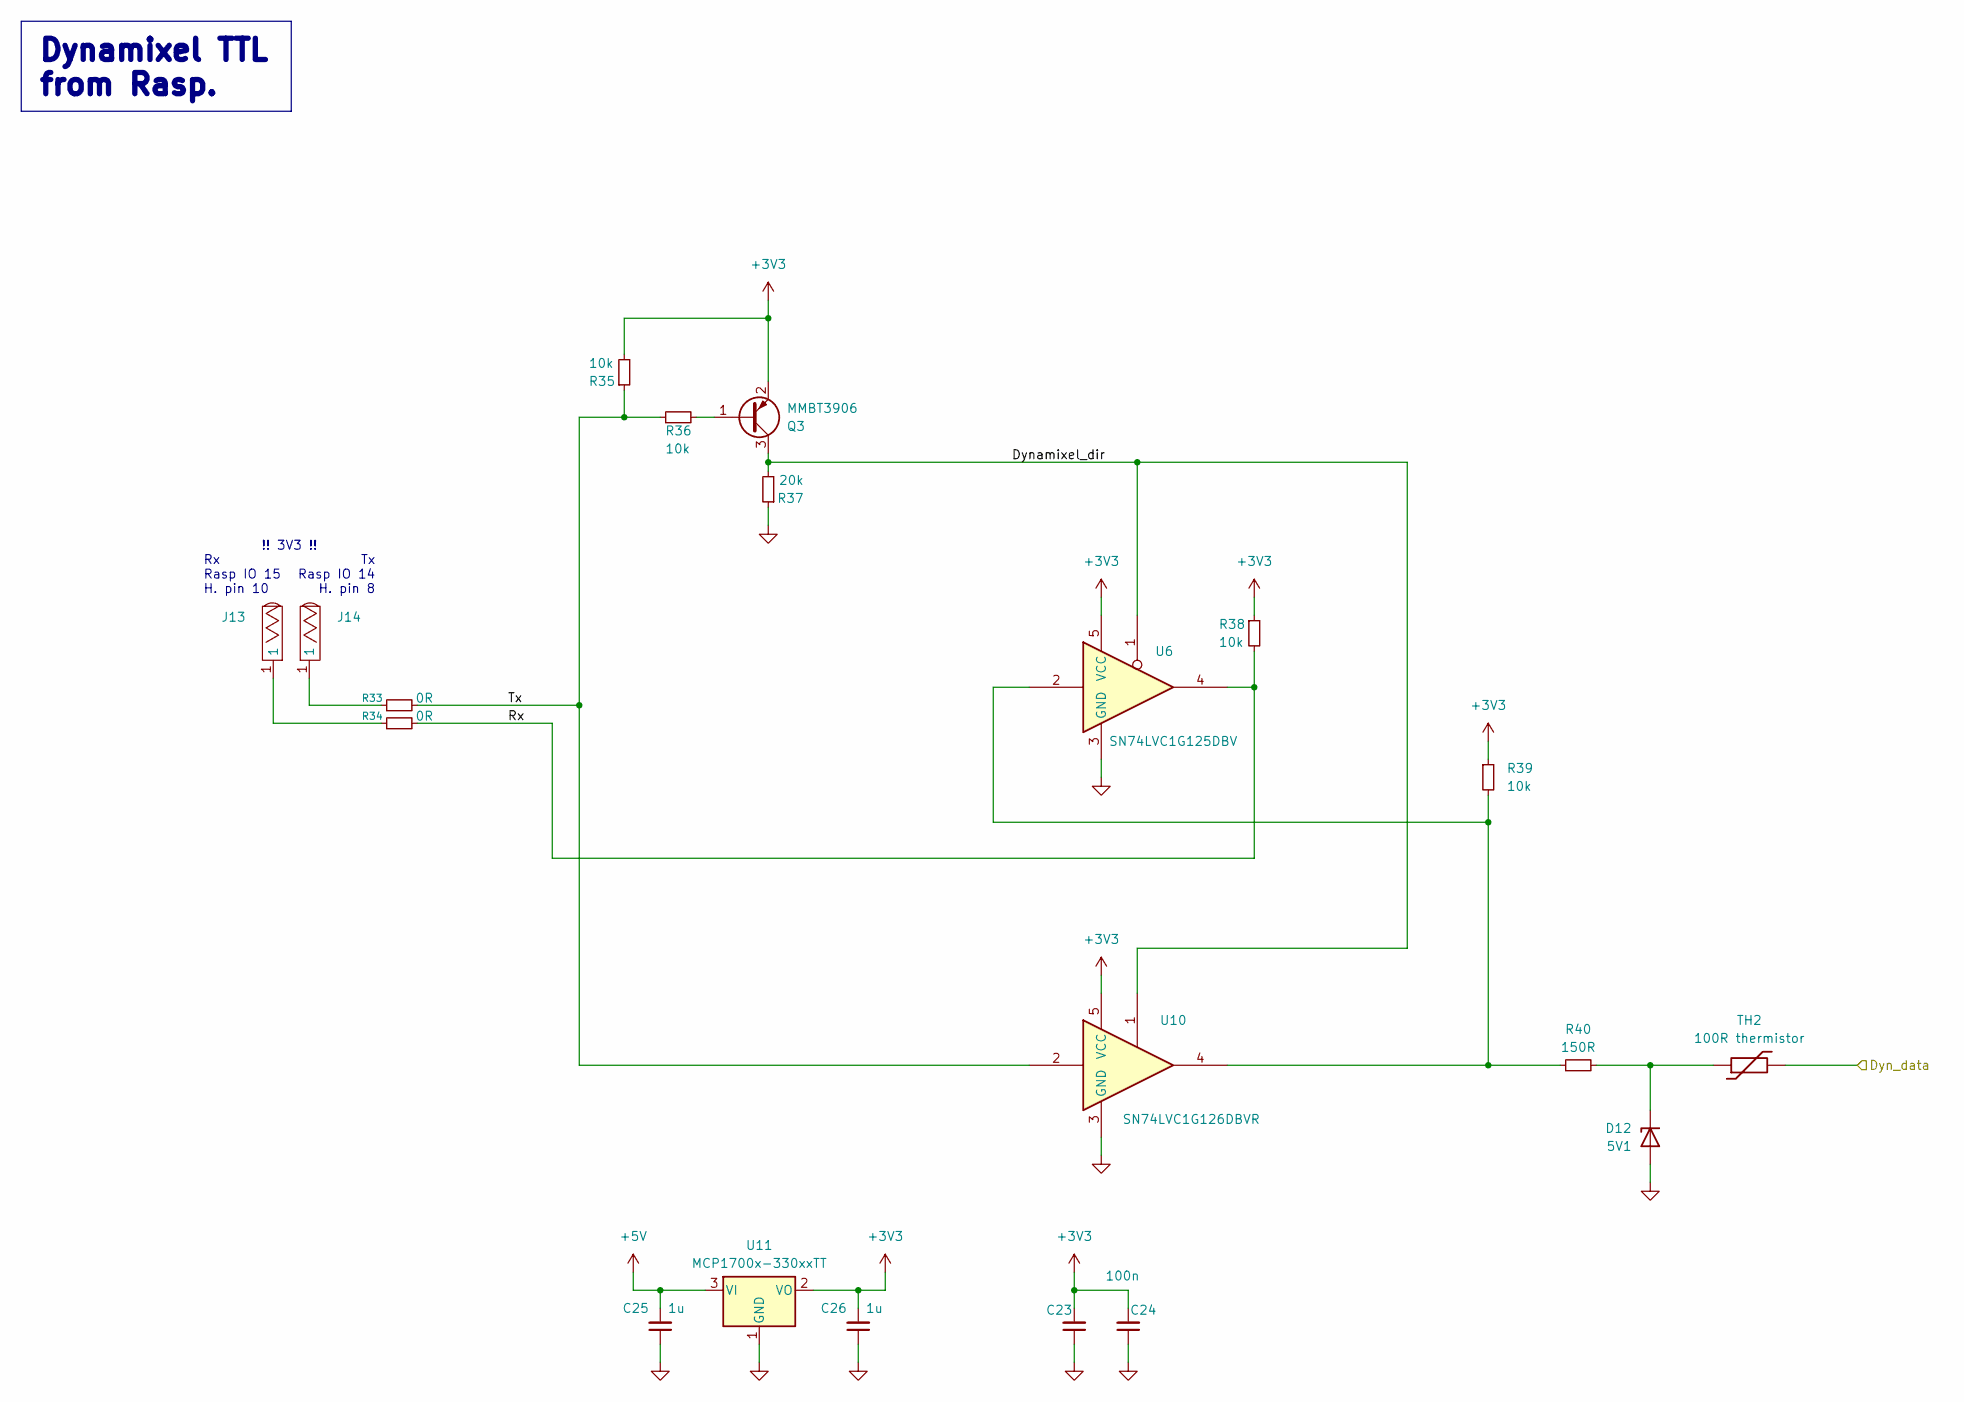
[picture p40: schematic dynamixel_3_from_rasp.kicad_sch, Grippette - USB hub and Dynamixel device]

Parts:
C23, C24: 100n; C_0603_1608Metric; LCSC Part C85864
C25, C26: 1u; C_0603_1608Metric; LCSC Part C1592
D12: 5V1; D_SOD-323; LCSC Part C151348
J13, J14: Pogo-pin 4mm; CONN-TH_YZ95315064P-01_pogo; LCSC Part C5157245
Q3: MMBT3906; SOT-23; LCSC Part C727128
R33, R34: 0R; R_0402_1005Metric; LCSC Part C17168
R35, R36, R38, R39: 10k; R_0402_1005Metric; LCSC Part C25744
R37: 20k; R_0402_1005Metric; LCSC Part C2906867
R40: 150R; R_0402_1005Metric; LCSC Part C138054
TH2: 100R thermistor; R_0603_1608Metric; LCSC Part C913703
U6: SN74LVC1G125DBV; SOT-23-5; LCSC Part C23654
U10: SN74LVC1G126DBVR; SOT-23-5; LCSC Part C7834
U11: MCP1700x-330xxTT; SOT-23; LCSC Part C39051

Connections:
+3V3: C23.2, C24.2, C26.2, Q3.2 (E), R35.2, R38.1, R39.1, U6.5 (VCC), U10.5 (VCC), U11.2 (VO)
+5V: C25.2, U11.3 (VI); also elsewhere on the board
/Dynamixel-TTL over USB/Dyn_data: TH2.2; also elsewhere on the board
/Dynamixel-TTL/Dynamixel_dir: Q3.3 (C), R37.2, U6.1, U10.1
/Dynamixel-TTL/Rx: R34.2, R38.2, U6.4
/Dynamixel-TTL/Tx: R33.2, R35.1, R36.1, U10.2
GND: C23.1, C24.1, C25.1, C26.1, D12.2 (A), R37.1, U6.3 (GND), U10.3 (GND), U11.1 (GND); also elsewhere on the board
unnamed: D12.1 (K), R40.2, TH2.1
unnamed: J13.1, R34.1
unnamed: J14.1, R33.1
unnamed: Q3.1 (B), R36.2
unnamed: R39.2, R40.1, U6.2, U10.4

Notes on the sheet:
Tx Rasp IO 14 H. pin 8
Rx Rasp IO 15 H. pin 10
!! 3V3 !!
Dynamixel TTL from Rasp.

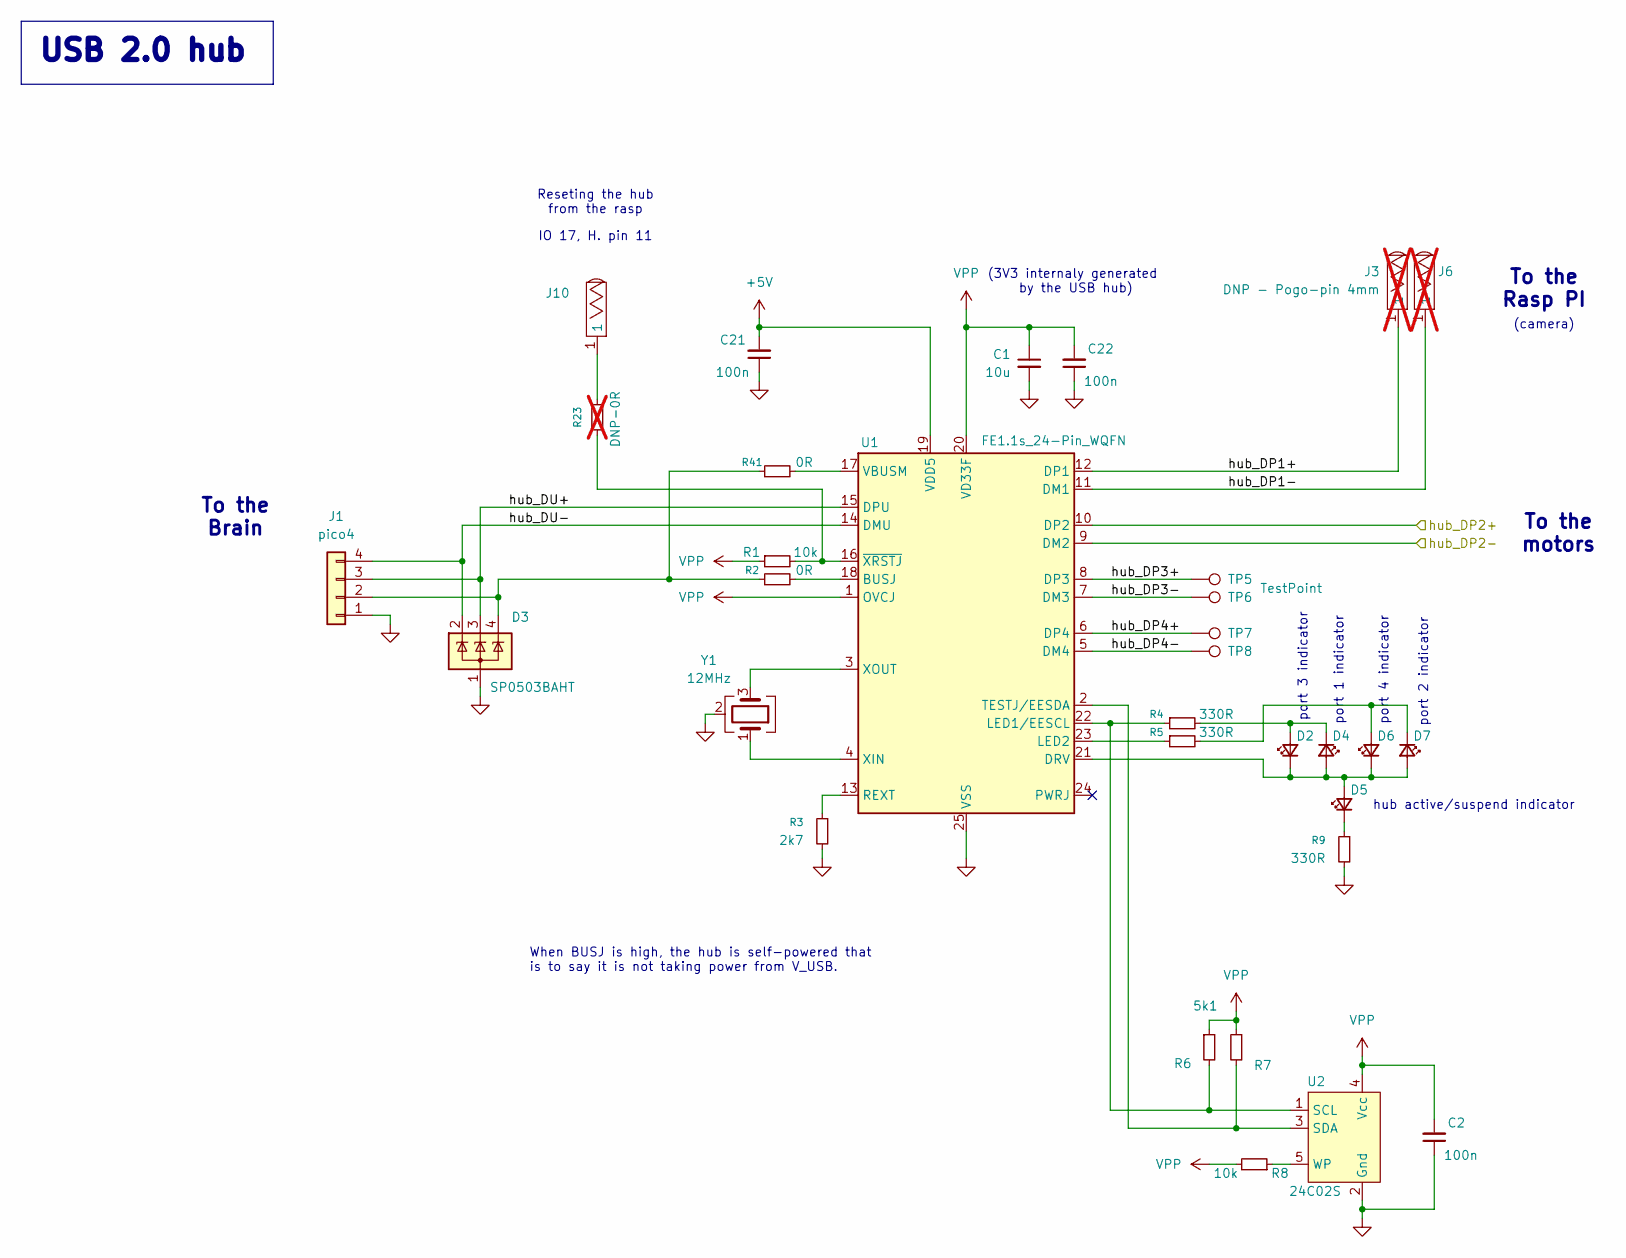
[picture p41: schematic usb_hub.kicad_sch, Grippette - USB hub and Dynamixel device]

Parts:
C1: 10u; C_0603_1608Metric; LCSC Part C1691
C2, C21, C22: 100n; C_0603_1608Metric; LCSC Part C85864
D2, D4, D6, D7: LED_Small; LED_0603_1608Metric; LCSC Part C7429915
D3: SP0503BAHT; SOT-143; LCSC Part C41364459
D5: LED_Small; LED_0603_1608Metric; LCSC Part C19171301
J1: pico4; Molex_PicoBlade_53047-0410_1x04_P1.25mm_Vertical; LCSC Part C504989
J3, J6: DNP - Pogo-pin 4mm; CONN-TH_YZ95315064P-01_pogo; LCSC Part C5157245; not fitted
J10: Pogo-pin 4mm; CONN-TH_YZ95315064P-01_pogo; LCSC Part C5157245
R1, R8: 10k; R_0402_1005Metric; LCSC Part C25744
R2, R41: 0R; R_0402_1005Metric; LCSC Part C17168
R3: 2k7; R_0402_1005Metric; LCSC Part C138017
R4, R5, R9: 330R; R_0402_1005Metric; LCSC Part C105875
R6, R7: 5k1; R_0402_1005Metric; LCSC Part C25905
R23: DNP-0R; R_0603_1608Metric; not fitted
TP5, TP6, TP7, TP8: TestPoint; TestPoint_Pad_D1.0mm
U1: FE1.1s_24-Pin_WQFN; WQFN-24-1EP_4x4mm_P0.5mm_EP2.6x2.6mm; LCSC Part C6776948
U2: 24C02S; SOT-23-5; LCSC Part C18723540
Y1: 12MHz; Crystal_SMD_3225-4Pin_3.2x2.5mm; LCSC Part C133334

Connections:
+5V: C21.2, U1.19 (VDD5); also elsewhere on the board
/Dynamixel-TTL over USB/hub_DP2+: U1.10 (DP2); also elsewhere on the board
/Dynamixel-TTL over USB/hub_DP2-: U1.9 (DM2); also elsewhere on the board
/USB hub/hub_DP1+: J3.1, U1.12 (DP1)
/USB hub/hub_DP1-: J6.1, U1.11 (DM1)
/USB hub/hub_DP3+: TP5.1, U1.8 (DP3)
/USB hub/hub_DP3-: TP6.1, U1.7 (DM3)
/USB hub/hub_DP4+: TP7.1, U1.6 (DP4)
/USB hub/hub_DP4-: TP8.1, U1.5 (DM4)
/USB hub/hub_DU+: D3.3 (K), J1.3, U1.15 (DPU)
/USB hub/hub_DU-: D3.2 (K), J1.4, U1.14 (DMU)
GND: C1.2, C2.1, C21.1, C22.1, D3.1 (A), J1.1, R3.2, R9.2, U1.25 (VSS), U2.2 (Gnd), Y1.2 (G), Y1.4 (G); also elsewhere on the board
unnamed: D2.2 (A), D4.1 (K), R4.2
unnamed: D2.1 (K), D4.2 (A), D5.2 (A), D6.1 (K), D7.2 (A), U1.21 (DRV)
unnamed: D5.1 (K), R9.1
unnamed: D6.2 (A), D7.1 (K), R5.2
unnamed: D3.4 (K), J1.2, R2.1, R41.1
unnamed: J10.1, R23.2
unnamed: R2.2, U1.18 (BUSJ)
unnamed: R4.1, R6.2, U1.22 (LED1/EESCL), U2.1 (SCL)
unnamed: R5.1, U1.23 (LED2)
unnamed: R3.1, U1.13 (REXT)
unnamed: R7.2, U1.2 (TESTJ/EESDA), U2.3 (SDA)
unnamed: R41.2, U1.17 (VBUSM)
unnamed: U1.4 (XIN), Y1.1
unnamed: U1.3 (XOUT), Y1.3
unnamed: R1.2, R23.1, U1.16 (~XRSTJ)
unnamed: R8.1, U2.5 (WP)
VPP: C1.1, C2.2, C22.2, R1.1, R6.1, R7.1, R8.2, U1.1 (OVCJ), U1.20 (VD33F), U2.4 (Vcc)

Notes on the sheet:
To the motors
port 4 indicator
When BUSJ is high, the hub is self-powered that is to say it is not taking power from V_USB.
port 2 indicator
port 3 indicator
To the Rasp PI
(3V3 internaly generated by the USB hub)
Reseting the hub from the rasp
(camera)
port 1 indicator
IO 17, H. pin 11
hub active/suspend indicator
To the Brain
USB 2.0 hub

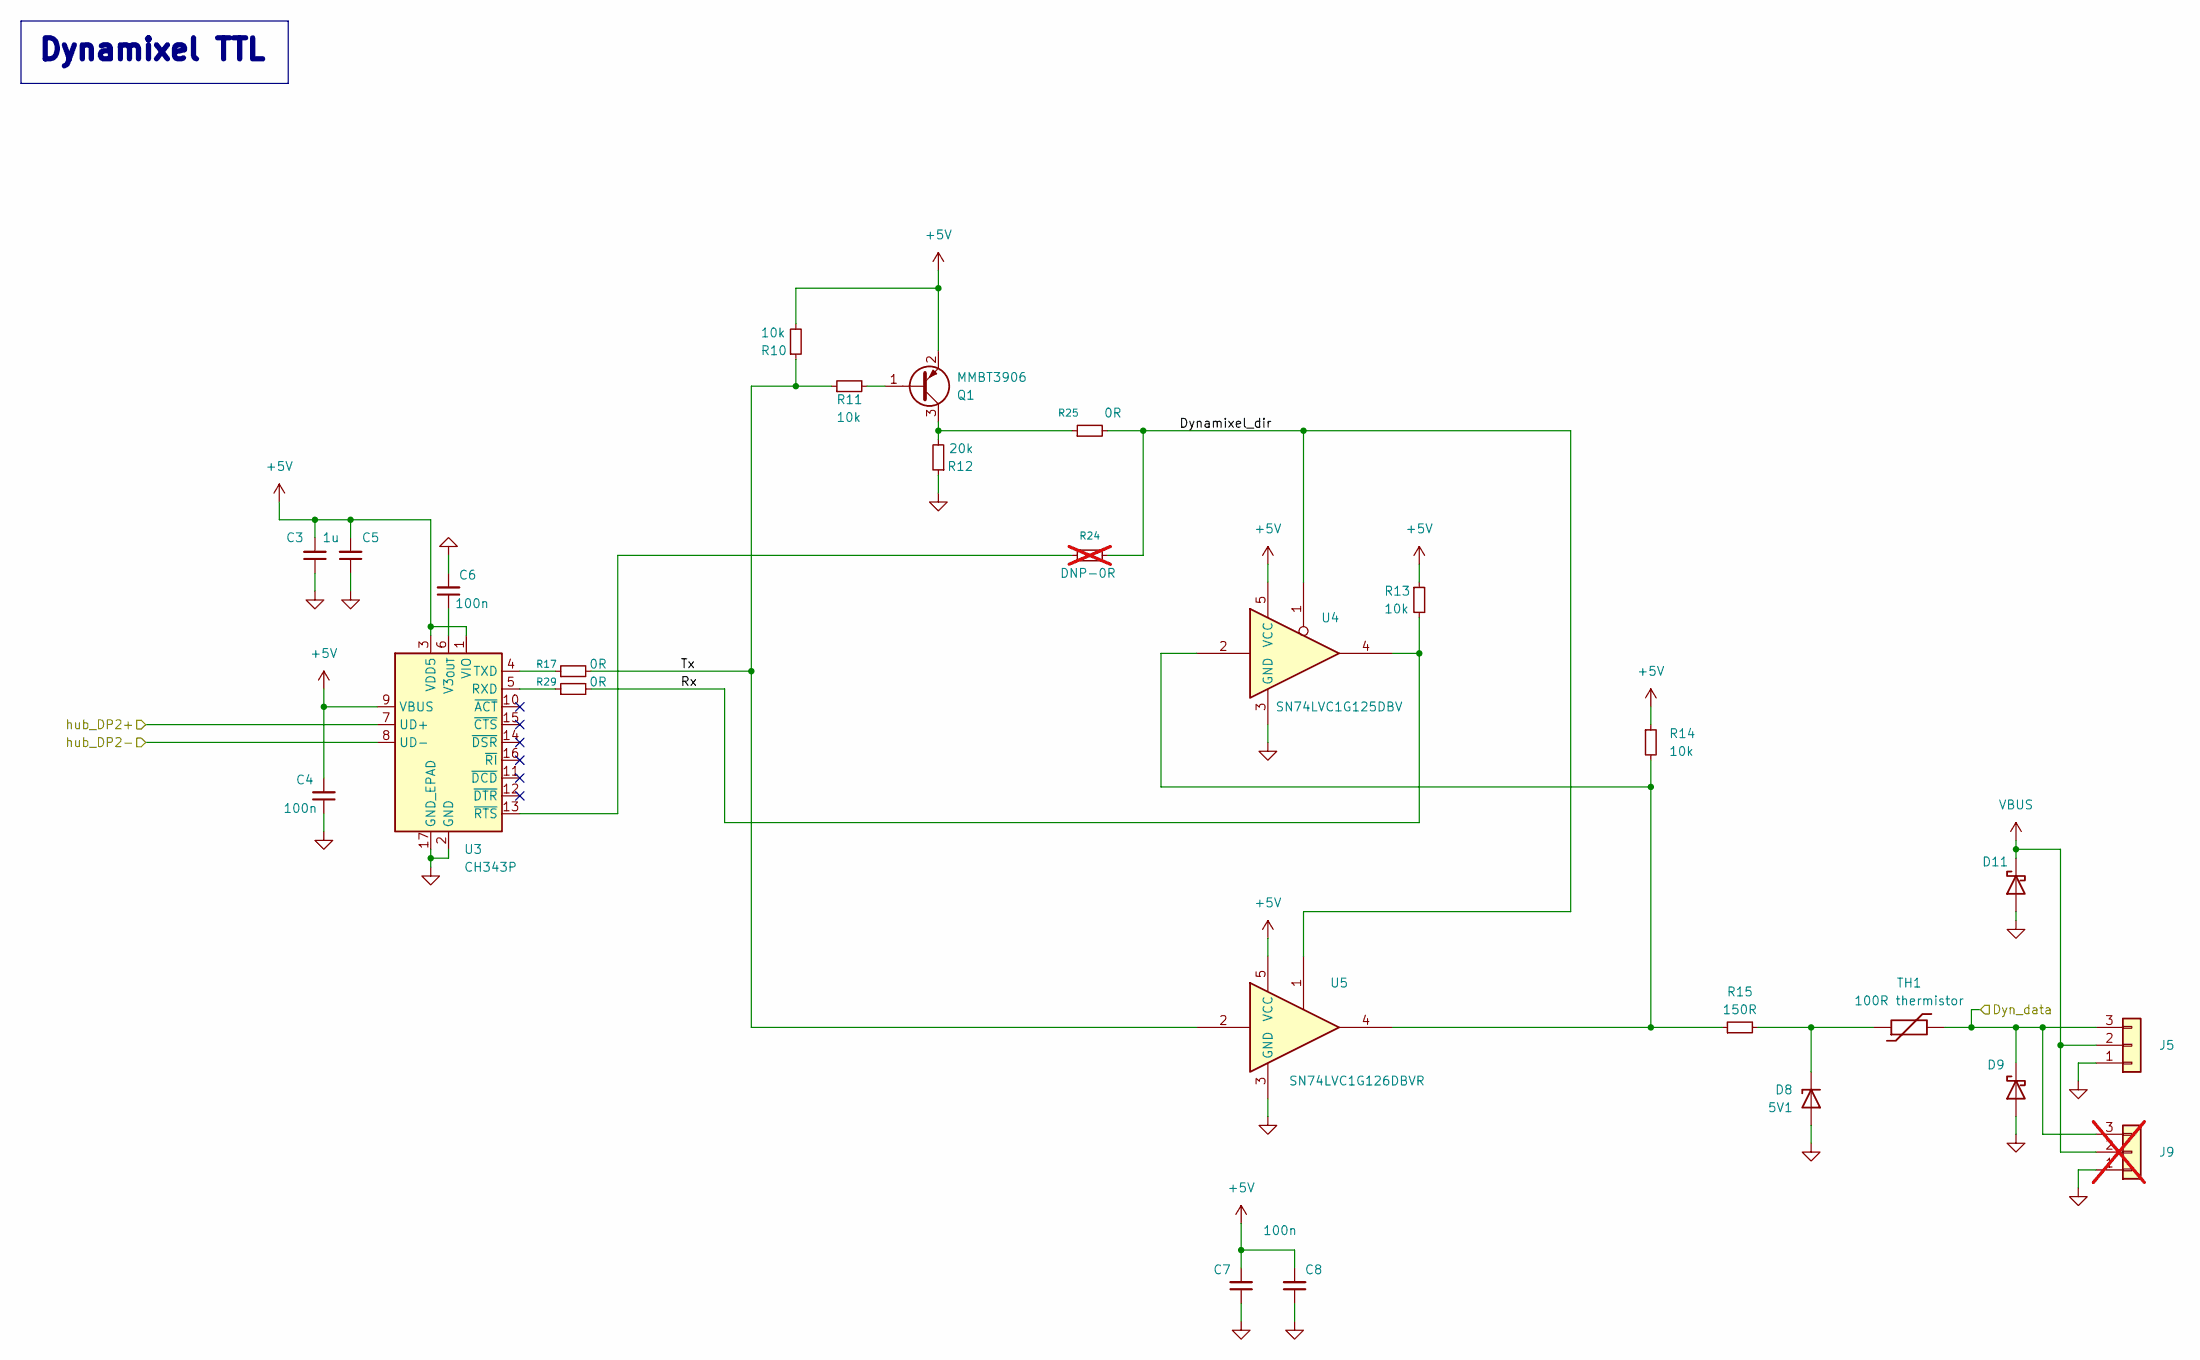
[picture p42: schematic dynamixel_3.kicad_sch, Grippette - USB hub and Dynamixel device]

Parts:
C3, C5: 1u; C_0603_1608Metric; LCSC Part C1592
C4, C6, C7, C8: 100n; C_0603_1608Metric; LCSC Part C85864
D8: 5V1; D_SOD-323; LCSC Part C151348
D9, D11: B5819WS; D_SOD-323; LCSC Part C64886
J5: Feetech; Molex_SPOX_5267-03A_1x03_P2.50mm_Vertical; LCSC Part C293315
J9: Feetech; Molex_SPOX_5267-03A_1x03_P2.50mm_Vertical; not fitted
Q1: MMBT3906; SOT-23; LCSC Part C727128
R10, R11, R13, R14: 10k; R_0402_1005Metric; LCSC Part C25744
R12: 20k; R_0402_1005Metric; LCSC Part C2906867
R15: 150R; R_0402_1005Metric; LCSC Part C138054
R17, R25, R29: 0R; R_0402_1005Metric; LCSC Part C17168
R24: DNP-0R; R_0603_1608Metric; not fitted
TH1: 100R thermistor; R_0603_1608Metric; LCSC Part C913703
U3: CH343P; WCH_QFN-16-1EP_3x3mm_P0.5mm_EP1.8x1.8mm; LCSC Part C2846043
U4: SN74LVC1G125DBV; SOT-23-5; LCSC Part C23654
U5: SN74LVC1G126DBVR; SOT-23-5; LCSC Part C7834

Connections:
+5V: C3.2, C4.2, C5.2, C7.2, C8.2, Q1.2 (E), R10.2, R13.1, R14.1, U3.1 (VIO), U3.3 (VDD5), U3.9 (VBUS), U4.5 (VCC), U5.5 (VCC); also elsewhere on the board
/Dynamixel-TTL over USB/Dyn_data: D9.1 (K), J5.3, J9.3, TH1.2; also elsewhere on the board
/Dynamixel-TTL over USB/Dynamixel_dir: R24.2, R25.2, U4.1, U5.1
/Dynamixel-TTL over USB/Rx: R13.2, R29.2, U4.4
/Dynamixel-TTL over USB/Tx: R10.1, R11.1, R17.2, U5.2
/Dynamixel-TTL over USB/hub_DP2+: U3.7 (UD+); also elsewhere on the board
/Dynamixel-TTL over USB/hub_DP2-: U3.8 (UD-); also elsewhere on the board
GND: C3.1, C4.1, C5.1, C6.2, C7.1, C8.1, D8.2 (A), D9.2 (A), D11.2 (A), J5.1, J9.1, R12.1, U3.2 (GND), U3.17 (GND_EPAD), U4.3 (GND), U5.3 (GND); also elsewhere on the board
unnamed: D8.1 (K), R15.2, TH1.1
unnamed: Q1.1 (B), R11.2
unnamed: Q1.3 (C), R12.2, R25.1
unnamed: R14.2, R15.1, U4.2, U5.4
unnamed: R29.1, U3.5 (RXD)
unnamed: R17.1, U3.4 (TXD)
unnamed: C6.1, U3.6 (V3_{OUT})
unnamed: R24.1, U3.13 (~RTS)
VBUS: D11.1 (K), J5.2, J9.2; also elsewhere on the board

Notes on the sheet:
Dynamixel TTL

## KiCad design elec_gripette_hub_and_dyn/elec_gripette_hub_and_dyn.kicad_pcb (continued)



Board: 4 copper layers, 65.0 x 30.0 mm, 122 parts (13 on the bottom side), 67 nets.

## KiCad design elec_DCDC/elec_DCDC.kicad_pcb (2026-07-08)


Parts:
C1, C2: 10u 35V; CP_Elec_6.3x7.7; LCSC Part C72488
C3: 22n; C_0402_1005Metric; LCSC Part C1532
C4: 100n; C_0402_1005Metric; LCSC Part C307331
C5, C6: 22u 16V; CP_Elec_4x5.4; LCSC Part C72502
C7: 100p 50V; C_0402_1005Metric; LCSC Part C106200
FID1, FID2, FID3: DNP Fiducial; Fiducial_1mm_Mask2mm
H1: PCB01196
H2: Logo HF 2025; Logo_HF_2025
H3: DNP Logo Pollen 2021; Logo_Pollen_2021_sq
H4, H5: Mounting Holes M2; MountingHole_2.2mm_M2_ISO7380_Pad_TopBottom
H6, H7: Centering Hole 2 mm; MountingHole_2.0mm
J1: XT30; AMASS_XT30PW-M_1x02_P2.50mm_Horizontal; LCSC Part C431092
J2: Dynamixel-3; JST_EH_B3B-EH-A_1x03_P2.50mm_Vertical; LCSC Part C160259
L1: 6,8u 3A; L_Bourns_SRN6045TA; LCSC Part C57254
R1: 10k; R_0402_1005Metric; LCSC Part C25744
R2: DNP-0R; R_0402_1005Metric; LCSC Part C17168; not fitted
R3: 0R; R_0402_1005Metric; LCSC Part C17168
R4: 120k; R_0402_1005Metric; LCSC Part C2909314
R5: 9k1; R_0402_1005Metric; LCSC Part C2909390
R6: 160k; R_0402_1005Metric; LCSC Part C25757
R7: 6k8; R_0402_1005Metric; LCSC Part C2906876
R8: 100k; R_0402_1005Metric; LCSC Part C2906883
R9: 51k; R_0402_1005Metric; LCSC Part C2909367
U1: MP2338; SOT-583-8_L2.1-W1.2-P0.50-LS1.6-BR; LCSC Part C7210174

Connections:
GND: C1.2, C2.2, C3.1, C5.2, C6.2, H4.1, H5.1, J1.1, J1.MP (MountPin), J2.1, R5.1, R7.1, R9.2, U1.4 (GND)
unnamed: C7.2, R1.2, R2.1, R3.1
unnamed: C1.1, C2.1, J1.2, U1.2 (VIN), U1.6 (EN)
unnamed: C5.1, C6.1, C7.1, J2.2, L1.1, R4.2, R6.2, R8.1
unnamed: R2.2, R4.1, R5.2
unnamed: R3.2, R6.1, R7.2
unnamed: C4.2, U1.5 (BST)
unnamed: R1.1, U1.8 (FB)
unnamed: R8.2, R9.1, U1.1 (PG)
unnamed: C3.2, U1.7 (SS)
unnamed: C4.1, L1.2, U1.3 (SW)

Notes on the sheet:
Date
Check
Release
Fiducials
ASE01197
12V
Initial drawing
"elec_DCDC" is a part of the Grabette/Gripette project, it is a small form-factor DCDC that lowers 24V from OpenArm to 12V for Dynamixel motors.
Todo: - ideal diode to avoid reverse supplying?
Nota: choose output voltage thanks to 0R. Default is 12V.
Designer
Comments
dd/mm/2026

Board: 2 copper layers, 29 parts (2 on the bottom side), 11 nets, no tracks yet.

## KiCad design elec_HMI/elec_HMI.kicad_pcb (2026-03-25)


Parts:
D1: Red; LED_0603_1608Metric; LCSC Part C84263
FID1, FID2, FID3: DNP Fiducial; Fiducial_1mm_Mask2mm
H1: PCB01192
H2: Logo HF 2025; Logo_HF_2025
H3: DNP Logo Pollen 2021; Logo_Pollen_2021_sq
H4, H5: Mounting Holes M2; MountingHole_2.2mm_M2_ISO7380_Pad_TopBottom
H6, H7: Centering Hole 2 mm; MountingHole_2.0mm
J1: JST SH; JST_SH_SM04B-SRSS-TB_1x04-1MP_P1.00mm_Horizontal; LCSC Part C160404
Q1: MMBT3906; SOT-23; LCSC Part C727128
R1: 10k; R_0402_1005Metric; LCSC Part C25744
R2, R4: 470R; R_0402_1005Metric; LCSC Part C25117
SW1: SW_SPST; KEY-TH_CPG135001D0X; LCSC Part C400229

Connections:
+3V3: J1.2, R1.1, R2.2
GND: H4.1, H5.1, J1.1, J1.MP (MountPin), Q1.3 (C), SW1.2 (B)
unnamed: D1.2 (A), R2.1
unnamed: D1.1 (K), Q1.2 (E)
unnamed: J1.3, R1.2, SW1.1 (A)
unnamed: J1.4, R4.2
unnamed: Q1.1 (B), R4.1

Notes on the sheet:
Date
Check
Release
Fiducials
ASE01193
Initial drawing
"elec_HMI" is a part of the Grabette/Gripette project, it gathers buttons and LEDs.
Designer
Comments
dd/mm/2026


Board: 2 copper layers, 38.0 x 20.0 mm, 16 parts (0 on the bottom side), 7 nets.

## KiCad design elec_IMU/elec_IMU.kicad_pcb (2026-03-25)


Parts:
C1, C2: 100n 6V3; C_0402_1005Metric; LCSC Part C1525
D1: SP0503BAHT; SOT-143; LCSC Part C41364459
FID1, FID2, FID3: DNP Fiducial; Fiducial_1mm_Mask2mm
G1: qwiic_Logo; Logo_qwiic_5mm
H1: PCB01190
H2: Logo HF 2025; Logo_HF_2025
H3: DNP Logo Pollen 2021; Logo_Pollen_2021_sq
H4, H5: Mounting Holes M2; MountingHole_2.2mm_M2_ISO7380_Pad_TopBottom
H6, H7: Centering Hole 2 mm; MountingHole_2.0mm
J1, J2: JST SH; JST_SH_SM04B-SRSS-TB_1x04-1MP_P1.00mm_Horizontal; LCSC Part C160404
R1, R2: 0R; R_0402_1005Metric; LCSC Part C17168
R3, R4: DNP-10k; R_0402_1005Metric; LCSC Part C25744; not fitted
TP1: TestPoint; TestPoint_Loop_D2.50mm_Drill1.0mm_LowProfile
U1: BMI088; Bosch_LGA-16_4.5x3mm_P0.5mm_LayoutBorder7x1y_ClockwisePinNu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; LCSC Part C194919

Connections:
+3V3: C1.1, C2.2, D1.2 (K), J1.2, J2.2, R3.1, R4.1, U1.3 (VDD), U1.7 (PS), U1.11 (VDDIO)
GND: C1.2, C2.1, D1.1 (A), H4.1, H5.1, J1.1, J1.MP (MountPin), J2.1, J2.MP (MountPin), R1.1, R2.1, U1.2 (GNDA), U1.4 (GNDA), U1.6 (GNDIO)
unnamed: D1.3 (K), J1.3, J2.3, R4.2, U1.9 (SDI/SDA)
unnamed: D1.4 (K), J1.4, J2.4, R3.2, U1.8 (SCK/SCL)
unnamed: TP1.1, U1.16 (INT1)
unnamed: R1.2, U1.15 (SDO1)
unnamed: R2.2, U1.10 (SDO2)

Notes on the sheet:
Date
Check
Release
STEMMA QT 1mm
Fiducials
ASE01191
3V3 Default
Initial drawing
"elec_IMU" is a part of the Grabette/Gripette project, it is a small form-factor IMU over Qwiic connector.
Designer
Comments
dd/mm/2026



Board: 2 copper layers, 20.0 x 20.0 mm, 21 parts (2 on the bottom side), 7 nets.

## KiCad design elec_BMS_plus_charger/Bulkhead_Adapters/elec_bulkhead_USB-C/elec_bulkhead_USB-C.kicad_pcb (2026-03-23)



Board: 2 copper layers, 14.0 x 14.0 mm, 9 parts (4 on the bottom side), 4 nets, no tracks yet.

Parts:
D3: ESD5Z6.0; D_SOD-523
H2: Logo HF 2025; Logo_HF_2025
H3: DNP Logo Pollen 2021; Logo_Pollen_2021_sq
H4, H5: Mounting Holes M2; MountingHole_2.2mm_M2_ISO7380_Pad_TopBottom
J1: JST EH 2; JST_EH_B2B-EH-A_1x02_P2.50mm_Vertical
J2: USB-C Rec. Vert.; USB-C_16p_vert_Shou-Han_TYPE-C 16P LTH6.8 - C5187468
R1, R2: 5k1; R_0402_1005Metric

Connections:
GND: D3.2 (A), H4.1, H5.1, J1.1, J2.A1 (GND), J2.A12 (GND), J2.B1 (GND), J2.B12 (GND), J2.S1 (SHIELD), R1.2, R2.2
unnamed: D3.1 (K), J1.2, J2.A4 (VBUS), J2.A9 (VBUS), J2.B4 (VBUS), J2.B9 (VBUS)
unnamed: J2.A5 (CC1), R1.1
unnamed: J2.B5 (CC2), R2.1

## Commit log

2026-03-12 [init] Initial commit
    [elec_angle_sensor.kicad_pcb, elec_angle_sensor.kicad_sch]
2026-03-12 [added] elec_IMU
    [elec_IMU.kicad_pcb, elec_IMU.kicad_sch]
2026-03-17 [update] Full schematic + positionning
    [elec_IMU.kicad_pcb, elec_IMU.kicad_sch, elec_angle_sensor.kicad_pcb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]
2026-03-17 [update] Angle+IMU are routed ERC OK
    [elec_HMI.kicad_pcb, elec_HMI.kicad_sch, elec_IMU.kicad_pcb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]
2026-03-17 [update] IMU + angle sensor RC1
    [ASE001189-A1_Grabette_elec_angle_sensor.step, ASE01191-A1_Grabette_elec_IMU.step, elec_HMI.kicad_sch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]
2026-03-17 [added] Wiring Diagrams
    [ASE01193_Grabette_elec_HMI_STEP.step, elec_HMI.kicad_pcb, elec_HMI.kicad_sch]
2026-03-18 [added] Gripette-specific DCDC
    [ASE001189-A1_Grabette_elec_angle_sensor.step, ASE01197_elec_DCDC.step, elec_DCDC.kicad_pcb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]
2026-03-20 [added] BMS/Charger
    [ASE001189-A1_elec_angle_sensor_STEP.step, elec_BMS_plus_charger.kicad_pcb, elec_BMS_plus_charger.kicad_sch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]
2026-03-23 [update] BMS schematic DRC 0k.
    [elec_bulkhead_USB-C.kicad_pcb, elec_bulkhead_USB-C.kicad_sch, power.kicad_sch]
2026-03-25 [update] Mechanical adaptations.
    [ASE01191-A1_Grabette_elec_IMU.step, ASE01193_Grabette_elec_HMI_STEP.step, elec_BMS_plus_charger.kicad_pcb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]
2026-03-25 [update] OK for JLC
    [elec_HMI.kicad_pcb, elec_HMI.kicad_sch, elec_IMU.kicad_pcb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]
2026-04-09 [added] Gripette USB hub + DCDC
    [DCDC.kicad_sch, dynamixel_3.kicad_sch, elec_gripette_hub_and_dyn.kicad_pcb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]
2026-04-10 [update] sch reviewed by Claude
    [DCDC.kicad_sch, dynamixel_3.kicad_sch, elec_gripette_hub_and_dyn.kicad_pcb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]
2026-04-15 [update] Gripette hub routed
    [DCDC.kicad_sch, dynamixel_3.kicad_sch, elec_HMI.kicad_sch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]
2026-04-15 [added] XT60-USB-C Bulkhead for Gripette, JLC ready.
    [bulkhead.dxf, elec_BMS_plus_charger.kicad_sch, elec_bulkhead_XT60_USB-C.kicad_pcb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]
2026-04-16 [update] Gripette bulkhead ready for production.
    [DCDC.kicad_sch, elec_bulkhead_XT60_USB-C.kicad_pcb, elec_bulkhead_XT60_USB-C.kicad_sch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]
2026-04-16 [uptate] Gripette hub ok for JLC
    [DCDC.kicad_sch, dynamixel_3.kicad_sch, elec_gripette_hub_and_dyn.kicad_pcb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]
2026-04-17 [update] Release A1, small batch @JLC
    [elec_gripette_hub_and_dyn.kicad_pcb, elec_gripette_hub_and_dyn.kicad_sch]
2026-04-29 [update] BMS+charger DRC OK
    [elec_BMS_plus_charger.kicad_pcb, elec_BMS_plus_charger.kicad_sch, elec_BMS_plus_charger.step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]
2026-05-03 [update] move BMS+charger to a dedicated repo.
    [elec_BMS_plus_charger.kicad_pcb, elec_BMS_plus_charger.kicad_sch, elec_BMS_plus_charger.step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]
2026-05-26 [update] Added error to gripette, going to B1
    [DCDC.kicad_sch, elec_angle_sensor.kicad_sch, elec_gripette_hub_and_dyn.kicad_sch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]
2026-05-28 [update] SCH B1-RC1
    [DCDC.kicad_sch, dynamixel_3.kicad_sch, elec_gripette_hub_and_dyn.kicad_pcb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]
2026-05-29 [update] SCH + PCB B1-RC1
    [DCDC.kicad_sch, dynamixel_3.kicad_sch, dynamixel_3_from_rasp.kicad_sch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]
2026-06-01 [update] Before review
    [dynamixel_3.kicad_sch, elec_gripette_hub_and_dyn.kicad_pcb, usb_hub.kicad_sch]
2026-06-01 [update] review by Claude. Corrections, RC2
    [DCDC.kicad_sch, dynamixel_3_from_rasp.kicad_sch, elec_gripette_hub_and_dyn.kicad_pcb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]
2026-06-02 [update] gripette + bulkhead -B1 in production @JLCPCB
    [ASE01199-B1_elec_bulkhead_XT60_USB-C_STEP.step, ASE01201-B1_elec_gripette_hub_and_dyn_STEP.step, DCDC.kicad_sch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]
2026-06-30 [fix] Ajusting cable length
    [CAB01206_Gripette_internal_power_cable.xlsx, CAB01207_Gripette_internal_data_cable.xlsx, elec_gripette_hub_and_dyn.kicad_sch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]
